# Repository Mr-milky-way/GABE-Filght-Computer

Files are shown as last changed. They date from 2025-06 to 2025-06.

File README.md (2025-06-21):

# G.A.B.E.-Filght-Computer
*Good Avionics, Bad Engineer*

## What is it?
The GABE flight computer is an open source rocket flight computer for controlling amateur or model rockets. It's a 4 layer PCB and pretty standard. It has a CoCom locked GPS, and 2 IMUs, a BMP390, 8 different servo header pins and can be powered off of a 12-26v battery. It uses and arm switch to power it on and has 6 pyro channels. It uses the MIMXRT1062DVJ6B with a teensy bootloader.



I tried to make it look nice but IDK, also that cad needs some work so thats why it's not shown.

> [!NOTE]
> The code is a demo of the Servos, LED, Pyros, and buzzer. This is so I have A low or very low ITAR risk. :)

## Why?
For aboout 3 years at this point I have wanted to make a Fin controlled rocket, and my first flight computter was, well a first. It didn't work really well and ended up frying itself via the servo PWM lines (I fixed that on this one with a level shifter). It was also large and bulky and the wire connectors were to small, not to mention it was ugly. So I set out to make this one.
I wanted it to look nice and work well and use mostly SMD parts, and for the most part I did.

## PICTURES




## BOM
Some parts have a value different from what it should be, this is because it was only one I could find. :)

| Part | Cost (all parts) | Count | Supplyer | Link | Part ID | Use | Value |
| --- | --- | ----- | --- | --- | --- | --- | --- |
| MIMXRT1062DVJ6B | $11.93 | 1 | Digikey  | [MIMXRT1062DVJ6B NXP USA Inc. \| Integrated Circuits (ICs) \| DigiKey](https://www.digikey.com/en/products/detail/nxp-usa-inc/MIMXRT1062DVJ6B/13574426) | U5 | MPU | |
| BNO055 | $12.34 | 1 | Digikey  | [BNO055 Bosch Sensortec \| Sensors, Transducers \| DigiKey](https://www.digikey.com/en/products/detail/bosch-sensortec/BNO055/6136301) | U1 | IMU | |
| TXB0108PWRG4 | $1.41 | 1 | Digikey  | [TXB0108PWRG4 Texas Instruments \| Integrated Circuits (ICs) \| DigiKey](https://www.digikey.com/en/products/detail/texas-instruments/TXB0108PWRG4/1910158) | U6 | Level Shifter | |
| RTAN0805BKE10K0 | $0.34 | 1 | Digikey  | [RTAN0805BKE10K0 Stackpole Electronics Inc \| Resistors \| DigiKey](https://www.digikey.com/en/products/detail/stackpole-electronics-inc/RTAN0805BKE10K0/6602188) | R1 | Resistor | 10KΩ |
| FC-135R 32.7680KF-A0 | $2.13 | 3 | Digikey  | [FC-135R 32.7680KF-A0 EPSON \| Crystals, Oscillators, Resonators \| DigiKey](https://www.digikey.com/en/products/detail/epson/FC-135R-32-7680KF-A0/5604247) | X1,X2,X4 | Crystal | 32.7680KHZ |
| CHV0805N250220FCT | $2.12 | 4 | Digikey  | [CHV0805N250220FCT Cal-Chip Electronics, Inc. \| Capacitors \| DigiKey](https://www.digikey.com/en/products/detail/cal-chip-electronics-inc/CHV0805N250220FCT/22155267) | C1,C2,C5,C6 | Capacitor | 22PF |
| CC0805KRX7R9BB104 | $0.48 | 6 | Digikey  | [CC0805KRX7R9BB104 YAGEO \| Capacitors \| DigiKey](https://www.digikey.com/en/products/detail/yageo/CC0805KRX7R9BB104/302874) | C3,C4,C7,C8,C11,C12 | Capacitor | 0.1UF |
| BNO085 | $13.05 | 1 | Digikey  | [BNO085 CEVA Technologies, Inc. \| Sensors, Transducers \| DigiKey](https://www.digikey.com/en/products/detail/ceva-technologies-inc/BNO085/9445940) | U2 | IMU | |
| BMP390 | $3.15 | 1 | Digikey  | [BMP390 Bosch Sensortec \| Sensors, Transducers \| DigiKey](https://www.digikey.com/en/products/detail/bosch-sensortec/BMP390/16164575) | U3 | | |
| NEO-M9N-00B | $27.00 | 1 | Digikey  | [NEO-M9N-00B u-blox \| RF and Wireless \| DigiKey](https://www.digikey.com/en/products/detail/u-blox/NEO-M9N-00B/12149174) | U4 | GPS | |
| CONSMA001-C-G | $2.79 | 1 | Digikey  | [CONSMA001-C-G TE Connectivity Linx \| Connectors, Interconnects \| DigiKey](https://www.digikey.com/en/products/detail/te-connectivity-linx/CONSMA001-C-G/11482824) | X3 | SMA connector | |
| RG0603R-330-D-T10 | $0.16 | 1 | Digikey  | [RG0603R-330-D-T10 Susumu \| Resistors \| DigiKey](https://www.digikey.com/en/products/detail/susumu/RG0603R-330-D-T10/18103232) | R2 | Resistor | 33Ω |
| BLM15PX121SN1D | $0.30 | 3 | Digikey  | [BLM15PX121SN1D Murata Electronics \| Filters \| DigiKey](https://www.digikey.com/en/products/detail/murata-electronics/BLM15PX121SN1D/4421095) | FB1-FB3 | Ferrite Bead | 120Ω |
| CC0805JRNPO9BN470 | $0.10 | 1 | Digikey  | [CC0805JRNPO9BN470 YAGEO \| Capacitors \| DigiKey](https://www.digikey.com/en/products/detail/yageo/CC0805JRNPO9BN470/302841) | C9 | Capacitor | 47PF |
| ML414H IV01E | $1.84 | 1 | Digikey  | [ML414H IV01E Seiko Instruments \| Battery Products \| DigiKey](https://www.digikey.com/en/products/detail/seiko-instruments/ML414H-IV01E/1889203) | BT1 | Battery Holder | |
| PMEG4005AEA-QX | $0.32 | 1 | Digikey  | [https://www.digikey.com/en/products/detail/nexperia-usa-inc/PMEG4005AEA-QX/17295512](https://www.digikey.com/en/products/detail/nexperia-usa-inc/PMEG4005AEA-QX/17295512) | D1 | Diode | |
| RG0603P-102-B-T10 | $0.20 | 1 | Digikey  | [RG0603P-102-B-T10 Susumu \| Resistors \| DigiKey](https://www.digikey.com/en/products/detail/susumu/RG0603P-102-B-T10/18103206) | R3 | Resistor | 1KΩ |
| C0805C105K9RACTU | $0.15 | 1 | Digikey  | [C0805C105K9RACTU KEMET \| Capacitors \| DigiKey](https://www.digikey.com/en/products/detail/kemet/C0805C105K9RACTU/2211772) | C10 | Capacitor | 1UF |
| BL-HBXJXGX32L | $0.50 | 1 | Digikey  | [BL-HBXJXGX32L American Bright Optoelectronics Corporation](https://www.digikey.com/en/products/detail/american-bright-optoelectronics-corporation/BL-HBXJXGX32L/9678124) | D2 | LED | |
| XRCGB24M000F3M00R0 | $0.30 | 1 | Digikey  | [](https://www.digikey.com/en/products/detail/murata-electronics/XRCGB24M000F3M00R0/2368376)[XRCGB24M000F3M00R0 Murata Electronics \| Crystals, Oscillators, Resonators \| DigiKey](https://www.digikey.com/en/products/detail/murata-electronics/XRCGB24M000F3M00R0/2368376) | Y1 | Crystal | 24MHZ |
| MLZ2012N4R7LT000 | $0.10 | 1 | Digikey  | [MLZ2012N4R7LT000 TDK Corporation \| Inductors, Coils, Chokes \| DigiKey](https://www.digikey.com/en/products/detail/tdk-corporation/MLZ2012N4R7LT000/2523498) | L1 | Inductor | 4.7UH |
| 112J-TDAR-R01 | $2.52 | 1 | Digikey  | [112J-TDAR-R01 ATTEND Technology \| Connectors, Interconnects \| DigiKey](https://www.digikey.com/en/products/detail/attend-technology/112J-TDAR-R01/17633874) | K1 | SD card holder | |
| BAT54CTB6_R1_00001 | $0.25 | 1 | Digikey  | [BAT54CTB6_R1_00001 Panjit International Inc. \| Discrete Semiconductor Products \| DigiKey](https://www.digikey.com/en/products/detail/panjit-international-inc/BAT54CTB6-R1-00001/15796775) | U$1 | Diode | |
| SKRPACE010 | $0.21 | 1 | Digikey  | [SKRPACE010 Alps Alpine \| Switches \| DigiKey](https://www.digikey.com/en/products/detail/alps-alpine/SKRPACE010/18115579) | S1 | Switch | |
| W25Q64JVXGIM | $1.20 | 1 | PJRC | [Bootloader Chip for DIY Teensy 4.0 & 4.1 Projects](https://www.pjrc.com/store/ic_mkl02_t4.html) | U9 | Flash Chip | |
| MKL02Z32 | $6.25 | 1 | PJRC | [Bootloader Chip for DIY Teensy 4.0 & 4.1 Projects](https://www.pjrc.com/store/ic_mkl02_t4.html) | U8 | Bootloader | |
| W25N01GVZEIG TR | $3.01 | 1 | Digikey  | [W25N01GVZEIG TR Winbond Electronics \| Integrated Circuits (ICs) \| DigiKey](https://www.digikey.com/en/products/detail/winbond-electronics/W25N01GVZEIG-TR/5803931) | U10 | Flash Chip | |
| SMTB-1240-S-R | $1.35 | 1 | Digikey  | [SMTB-1240-S-R PUI Audio, Inc. \| Audio Products \| DigiKey](https://www.digikey.com/en/products/detail/pui-audio-inc/SMTB-1240-S-R/13165906) | LS1 | Buzzer | |
| IRLML6344TRPBF | $2.10 | 6 | Digikey  | [IRLML6344TRPBF Infineon Technologies \| Discrete Semiconductor Products \| DigiKey](https://www.digikey.com/en/products/detail/infineon-technologies/IRLML6344TRPBF/2538152) | Q2-Q7 | Mosfet | |
| LM7805MPX/NOPB | $1.38 | 1 | Digikey  | [LM7805MPX/NOPB Texas Instruments \| Integrated Circuits (ICs) \| DigiKey](https://www.digikey.com/en/products/detail/texas-instruments/LM7805MPX-NOPB/6110583) | VR1 | Voltage Reguator | |
| TLV75533PDBVR | $0.32 | 1 | Digikey  | [TLV75533PDBVR Texas Instruments \| Integrated Circuits (ICs) \| DigiKey](https://www.digikey.com/en/products/detail/texas-instruments/TLV75533PDBVR/9356541) | U7 | Voltage Reguator | |
| AK100/2DS-5.0-V-GREY | $5.64 | 12 | Digikey  | [https://www.digikey.com/en/products/detail/ptr-hartmann/AK100-2DS-5-0-V-GREY/24787150](https://www.digikey.com/en/products/detail/ptr-hartmann/AK100-2DS-5-0-V-GREY/24787150) | U$2-U$13 | Terminal Block | |
| GCJ21BL8YA224KA01L | $3.52 | 11 | Digikey  | [GCJ21BL8YA224KA01L Murata Electronics \| Capacitors \| DigiKey](https://www.digikey.com/en/products/detail/murata-electronics/GCJ21BL8YA224KA01L/11618469) | C13,C14,C17,C18,C20,C23,C26,C31,C33,C34,C36 | Capacitor | .22UF |
| C0805C200J3HACAUTO | $0.26 | 2 | Digikey  | [C0805C200J3HACAUTO KEMET \| Capacitors \| DigiKey](https://www.digikey.com/en/products/detail/kemet/C0805C200J3HACAUTO/7958823) | C15,C16 | Capacitor | 20PF |
| GRM21BR61H475KE51L | $0.95 | 5 | Digikey  | [GRM21BR61H475KE51L Murata Electronics \| Capacitors \| DigiKey](https://www.digikey.com/en/products/detail/murata-electronics/GRM21BR61H475KE51L/4905540) | C19,C21,C24,C27,C30 | Capacitor | 4.7UF |
| CGA4J1X7R1V225K125AC | $0.46 | 1 | Digikey  | [CGA4J1X7R1V225K125AC TDK Corporation \| Capacitors \| DigiKey](https://www.digikey.com/en/products/detail/tdk-corporation/CGA4J1X7R1V225K125AC/2672856) | C25 | Capacitor | 2.2UF |
| CC0805KRX7R8BB103 | $0.10 | 1 | Digikey  | [CC0805KRX7R8BB103 YAGEO \| Capacitors \| DigiKey](https://www.digikey.com/en/products/detail/yageo/CC0805KRX7R8BB103/5884212) | C22 | Capacitor | 10NF |
| GRM21BR6YA106KE43L | $1.36 | 4 | Digikey  | [GRM21BR6YA106KE43L Murata Electronics \| Capacitors \| DigiKey](https://www.digikey.com/en/products/detail/murata-electronics/GRM21BR6YA106KE43L/5027598) | C28,C29,C32,C35 | Capacitor | 10UF |
| C0805C120J3GACTU | $0.44 | 2 | Digikey  | [C0805C120J3GACTU KEMET \| Capacitors \| DigiKey](https://www.digikey.com/en/products/detail/kemet/C0805C120J3GACTU/7388391) | C37,C38 | Capacitor | 12pF |
| UJ2-MIBH-G-SMT-TR | $0.44 | 1 | Digikey  | [UJ2-MIBH-G-SMT-TR Same Sky (Formerly CUI Devices) \| Connectors, Interconnects \| DigiKey](https://www.digikey.com/en/products/detail/same-sky-formerly-cui-devices/UJ2-MIBH-G-SMT-TR/13680627) | J1 | USB Con | |
| B4B-XH-A | $0.17 | 1 | Digikey  | [B4B-XH-A JST Sales America Inc. \| Connectors, Interconnects \| DigiKey](https://www.digikey.com/en/products/detail/jst-sales-america-inc/B4B-XH-A/1651047) | J2 | JST Con | |
| 61300311121 | $0.96 | 8 | Digikey  | https://www.digikey.com/en/products/detail/würth-elektronik/61300311121/4846825 | M1-M8 | Header pins | |
| DMG2305UX-7 | $0.18 | 1 | Digikey  | [DMG2305UX-7 Diodes Incorporated \| Discrete Semiconductor Products \| DigiKey](https://www.digikey.com/en/products/detail/diodes-incorporated/DMG2305UX-7/4340667) | Q1 | Mosfet | |
| SDR10EZPF2201 | $0.44 | 2 | Digikey  | [SDR10EZPF2201 Rohm Semiconductor \| Resistors \| DigiKey](https://www.digikey.com/en/products/detail/rohm-semiconductor/SDR10EZPF2201/16179905) | R4,R5 | Resistor | 2.2kΩ |
| SDR10EZPF1003 | $0.44 | 2 | Digikey  | [SDR10EZPF1003 Rohm Semiconductor \| Resistors \| DigiKey](https://www.digikey.com/en/products/detail/rohm-semiconductor/SDR10EZPF1003/17140208) | R6,R7 | Resistor | 100kΩ |
| SDR10EZPF2204 | $0.22 | 1 | Digikey  | [SDR10EZPF2204 Rohm Semiconductor \| Resistors \| DigiKey](https://www.digikey.com/en/products/detail/rohm-semiconductor/SDR10EZPF2204/19531048) | R8 | Resistor | 2.2MΩ |
| SDR10EZPF1R00 | $1.54 | 7 | Digikey  | [SDR10EZPF1R00 Rohm Semiconductor \| Resistors \| DigiKey](https://www.digikey.com/en/products/detail/rohm-semiconductor/SDR10EZPF1R00/16179859) | R9,R13,R15,R17,R19,R21,R23 | Resistor | 1Ω |
| RLT1220-F-5R00-FNH | $0.47 | 1 | Digikey  | [RLT1220-F-5R00-FNH Delta Electronics/Cyntec \| Resistors \| DigiKey](https://www.digikey.com/en/products/detail/delta-electronics-cyntec/RLT1220-F-5R00-FNH/9762198) | R10 | Resistor | 5Ω |
| RK73H2ATTD64R9F | $0.10 | 1 | Digikey  | [RK73H2ATTD64R9F KOA Speer Electronics, Inc. \| Resistors \| DigiKey](https://www.digikey.com/en/products/detail/koa-speer-electronics-inc/RK73H2ATTD64R9F/10228485?) | R11 | Resistor | 65Ω (64.9) |
| SDR10EZPF4700 | $1.32 | 6 | Digikey  | [SDR10EZPF4700 Rohm Semiconductor \| Resistors \| DigiKey](https://www.digikey.com/en/products/detail/rohm-semiconductor/SDR10EZPF4700/17140152) | R12,R14,R16,R18,R20,R22 | Resistor | 470Ω |
| RT0805BRD07723RL | $0.17 | 1 | Digikey  | [RT0805BRD07723RL YAGEO \| Resistors \| DigiKey](https://www.digikey.com/en/products/detail/yageo/RT0805BRD07723RL/7708570) | R24 | Resistor | 722Ω (723) |
| RK73H2ATTD1691F | $0.10 | 1 | Digikey  | [RK73H2ATTD1691F KOA Speer Electronics, Inc. \| Resistors \| DigiKey](https://www.digikey.com/en/products/detail/koa-speer-electronics-inc/RK73H2ATTD1691F/10234184) | R25 | Resistor | 1700Ω (1.69k) |
| COST OF MAIN PCB AND SMD-Stencil | $81.42 | 1 | PCB Way  | | | PCB | |
| TOTAL | $200.00 | 120 | | | | | |

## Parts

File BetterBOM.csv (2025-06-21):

Part | Cost (all parts) | Count | Supplyer | Link | Part ID | Use | Value
MIMXRT1062DVJ6B | $11.93 | 1 | Digikey | MIMXRT1062DVJ6B NXP USA Inc. | Integrated Circuits (ICs) | DigiKey | U5 | MPU
BNO055 | $12.34 | 1 | Digikey | BNO055 Bosch Sensortec | Sensors, Transducers | DigiKey | U1 | IMU
TXB0108PWRG4 | $1.41 | 1 | Digikey | TXB0108PWRG4 Texas Instruments | Integrated Circuits (ICs) | DigiKey | U6 | Level Shifter
RTAN0805BKE10K0 | $0.34 | 1 | Digikey | RTAN0805BKE10K0 Stackpole Electronics Inc | Resistors | DigiKey | R1 | Resistor | 10KΩ
FC-135R 32.7680KF-A0 | $2.13 | 3 | Digikey | FC-135R 32.7680KF-A0 EPSON | Crystals, Oscillators, Resonators | DigiKey | X1,X2,X4 | Crystal | 32.7680KHZ
CHV0805N250220FCT | $2.12 | 4 | Digikey | CHV0805N250220FCT Cal-Chip Electronics, Inc. | Capacitors | DigiKey | C1,C2,C5,C6 | Capacitor | 22PF
CC0805KRX7R9BB104 | $0.48 | 6 | Digikey | CC0805KRX7R9BB104 YAGEO | Capacitors | DigiKey | C3,C4,C7,C8,C11,C12 | Capacitor | 0.1UF
BNO085 | $13.05 | 1 | Digikey | BNO085 CEVA Technologies, Inc. | Sensors, Transducers | DigiKey | U2 | IMU
BMP390 | $3.15 | 1 | Digikey | BMP390 Bosch Sensortec | Sensors, Transducers | DigiKey | U3
NEO-M9N-00B | $27.00 | 1 | Digikey | NEO-M9N-00B u-blox | RF and Wireless | DigiKey | U4 | GPS
CONSMA001-C-G | $2.79 | 1 | Digikey | CONSMA001-C-G TE Connectivity Linx | Connectors, Interconnects | DigiKey | X3 | SMA connector
RG0603R-330-D-T10 | $0.16 | 1 | Digikey | RG0603R-330-D-T10 Susumu | Resistors | DigiKey | R2 | Resistor | 33Ω
BLM15PX121SN1D | $0.30 | 3 | Digikey | BLM15PX121SN1D Murata Electronics | Filters | DigiKey | FB1-FB3 | Ferrite Bead | 120Ω
CC0805JRNPO9BN470 | $0.10 | 1 | Digikey | CC0805JRNPO9BN470 YAGEO | Capacitors | DigiKey | C9 | Capacitor | 47PF
ML414H IV01E | $1.84 | 1 | Digikey | ML414H IV01E Seiko Instruments | Battery Products | DigiKey | BT1 | Battery Holder
PMEG4005AEA-QX | $0.32 | 1 | Digikey | https://www.digikey.com/en/products/detail/nexperia-usa-inc/PMEG4005AEA-QX/17295512 | D1 | Diode
RG0603P-102-B-T10 | $0.20 | 1 | Digikey | RG0603P-102-B-T10 Susumu | Resistors | DigiKey | R3 | Resistor | 1KΩ
C0805C105K9RACTU | $0.15 | 1 | Digikey | C0805C105K9RACTU KEMET | Capacitors | DigiKey | C10 | Capacitor | 1UF
BL-HBXJXGX32L | $0.50 | 1 | Digikey | BL-HBXJXGX32L American Bright Optoelectronics Corporation | D2 | LED
XRCGB24M000F3M00R0 | $0.30 | 1 | Digikey | XRCGB24M000F3M00R0 Murata Electronics | Crystals, Oscillators, Resonators | DigiKey | Y1 | Crystal | 24MHZ
MLZ2012N4R7LT000 | $0.10 | 1 | Digikey | MLZ2012N4R7LT000 TDK Corporation | Inductors, Coils, Chokes | DigiKey | L1 | Inductor | 4.7UH
112J-TDAR-R01 | $2.52 | 1 | Digikey | 112J-TDAR-R01 ATTEND Technology | Connectors, Interconnects | DigiKey | K1 | SD card holder
BAT54CTB6_R1_00001 | $0.25 | 1 | Digikey | BAT54CTB6_R1_00001 Panjit International Inc. | Discrete Semiconductor Products | DigiKey | U$1 | Diode
SKRPACE010 | $0.21 | 1 | Digikey | SKRPACE010 Alps Alpine | Switches | DigiKey | S1 | Switch
W25Q64JVXGIM | $1.20 | 1 | PJRC | Bootloader Chip for DIY Teensy 4.0 & 4.1 Projects | U9 | Flash Chip
MKL02Z32 | $6.25 | 1 | PJRC | Bootloader Chip for DIY Teensy 4.0 & 4.1 Projects | U8 | Bootloader
W25N01GVZEIG TR | $3.01 | 1 | Digikey | W25N01GVZEIG TR Winbond Electronics | Integrated Circuits (ICs) | DigiKey | U10 | Flash Chip
SMTB-1240-S-R | $1.35 | 1 | Digikey | SMTB-1240-S-R PUI Audio, Inc. | Audio Products | DigiKey | LS1 | Buzzer
IRLML6344TRPBF | $2.10 | 6 | Digikey | IRLML6344TRPBF Infineon Technologies | Discrete Semiconductor Products | DigiKey | Q2-Q7 | Mosfet
LM7805MPX/NOPB | $1.38 | 1 | Digikey | LM7805MPX/NOPB Texas Instruments | Integrated Circuits (ICs) | DigiKey | VR1 | Voltage Reguator
TLV75533PDBVR | $0.32 | 1 | Digikey | TLV75533PDBVR Texas Instruments | Integrated Circuits (ICs) | DigiKey | U7 | Voltage Reguator
AK100/2DS-5.0-V-GREY | $5.64 | 12 | Digikey | https://www.digikey.com/en/products/detail/ptr-hartmann/AK100-2DS-5-0-V-GREY/24787150 | U$2-U$13 | Terminal Block
GCJ21BL8YA224KA01L | $3.52 | 11 | Digikey | GCJ21BL8YA224KA01L Murata Electronics | Capacitors | DigiKey | C13,C14,C17,C18,C20,C23,C26,C31,C33,C34,C36 | Capacitor | .22UF
C0805C200J3HACAUTO | $0.26 | 2 | Digikey | C0805C200J3HACAUTO KEMET | Capacitors | DigiKey | C15,C16 | Capacitor | 20PF
GRM21BR61H475KE51L | $0.95 | 5 | Digikey | GRM21BR61H475KE51L Murata Electronics | Capacitors | DigiKey | C19,C21,C24,C27,C30 | Capacitor | 4.7UF
CGA4J1X7R1V225K125AC | $0.46 | 1 | Digikey | CGA4J1X7R1V225K125AC TDK Corporation | Capacitors | DigiKey | C25 | Capacitor | 2.2UF
CC0805KRX7R8BB103 | $0.10 | 1 | Digikey | CC0805KRX7R8BB103 YAGEO | Capacitors | DigiKey | C22 | Capacitor | 10NF
GRM21BR6YA106KE43L | $1.36 | 4 | Digikey | GRM21BR6YA106KE43L Murata Electronics | Capacitors | DigiKey | C28,C29,C32,C35 | Capacitor | 10UF
C0805C120J3GACTU | $0.44 | 2 | Digikey | C0805C120J3GACTU KEMET | Capacitors | DigiKey | C37,C38 | Capacitor | 12pF
UJ2-MIBH-G-SMT-TR | $0.44 | 1 | Digikey | UJ2-MIBH-G-SMT-TR Same Sky (Formerly CUI Devices) | Connectors, Interconnects | DigiKey | J1 | USB Con
B4B-XH-A | $0.17 | 1 | Digikey | B4B-XH-A JST Sales America Inc. | Connectors, Interconnects | DigiKey | J2 | JST Con
61300311121 | $0.96 | 8 | Digikey | https://www.digikey.com/en/products/detail/würth-elektronik/61300311121/4846825 | M1-M8 | Header pins
DMG2305UX-7 | $0.18 | 1 | Digikey | DMG2305UX-7 Diodes Incorporated | Discrete Semiconductor Products | DigiKey | Q1 | Mosfet
SDR10EZPF2201 | $0.44 | 2 | Digikey | SDR10EZPF2201 Rohm Semiconductor | Resistors | DigiKey | R4,R5 | Resistor | 2.2kΩ
SDR10EZPF1003 | $0.44 | 2 | Digikey | SDR10EZPF1003 Rohm Semiconductor | Resistors | DigiKey | R6,R7 | Resistor | 100kΩ
SDR10EZPF2204 | $0.22 | 1 | Digikey | SDR10EZPF2204 Rohm Semiconductor | Resistors | DigiKey | R8 | Resistor | 2.2MΩ
SDR10EZPF1R00 | $1.54 | 7 | Digikey | SDR10EZPF1R00 Rohm Semiconductor | Resistors | DigiKey | R9,R13,R15,R17,R19,R21,R23 | Resistor | 1Ω
RLT1220-F-5R00-FNH | $0.47 | 1 | Digikey | RLT1220-F-5R00-FNH Delta Electronics/Cyntec | Resistors | DigiKey | R10 | Resistor | 5Ω
RK73H2ATTD64R9F | $0.10 | 1 | Digikey | RK73H2ATTD64R9F KOA Speer Electronics, Inc. | Resistors | DigiKey | R11 | Resistor | 65Ω (64.9)
SDR10EZPF4700 | $1.32 | 6 | Digikey | SDR10EZPF4700 Rohm Semiconductor | Resistors | DigiKey | R12,R14,R16,R18,R20,R22 | Resistor | 470Ω
RT0805BRD07723RL | $0.17 | 1 | Digikey | RT0805BRD07723RL YAGEO | Resistors | DigiKey | R24 | Resistor | 722Ω (723)
RK73H2ATTD1691F | $0.10 | 1 | Digikey | RK73H2ATTD1691F KOA Speer Electronics, Inc. | Resistors | DigiKey | R25 | Resistor | 1700Ω (1.69k)
COST OF MAIN PCB AND SMD-Stencil | $81.42 | 1 | PCB Way |  |  | PCB
TOTAL | $200.00 | 120

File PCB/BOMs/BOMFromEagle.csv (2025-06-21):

Part | Value | Device | Package | Description
BT1 | RELOWABLE_BATTERY_ML414H | RELOWABLE_BATTERY_ML414H | ML414H_IV01E | SEIKO Reflowable Lithium Batteries
C1 | 22pF | 1.0UF-0805-25V-10% | 805 | ceramic capacitors
C2 | 22pF | 1.0UF-0805-25V-10% | 805 | ceramic capacitors
C3 | 0.1uF | 1.0UF-0805-25V-10% | 805 | ceramic capacitors
C4 | 0.1uF | 1.0UF-0805-25V-10% | 805 | ceramic capacitors
C5 | 22pF | 1.0UF-0805-25V-10% | 805 | ceramic capacitors
C6 | 22pF | 1.0UF-0805-25V-10% | 805 | ceramic capacitors
C7 | 0.1uF | 1.0UF-0805-25V-10% | 805 | ceramic capacitors
C8 | 0.1uF | 1.0UF-0805-25V-10% | 805 | ceramic capacitors
C9 | 47pF | 1.0UF-0805-25V-10% | 805 | ceramic capacitors
C10 | 1.0uF | 1.0UF-0805-25V-10% | 805 | ceramic capacitors
C11 | 0.1uF | 1.0UF-0805-25V-10% | 805 | ceramic capacitors
C12 | 0.1uF | 1.0UF-0805-25V-10% | 805 | ceramic capacitors
C13 | 0.22uF | 1.0UF-0805-25V-10% | 805 | ceramic capacitors
C14 | 0.22uF | 1.0UF-0805-25V-10% | 805 | ceramic capacitors
C15 | 20pF | 1.0UF-0805-25V-10% | 805 | ceramic capacitors
C16 | 20pF | 1.0UF-0805-25V-10% | 805 | ceramic capacitors
C17 | 0.22uF | 1.0UF-0805-25V-10% | 805 | ceramic capacitors
C18 | 0.22uF | 1.0UF-0805-25V-10% | 805 | ceramic capacitors
C19 | 4.7uF | 1.0UF-0805-25V-10% | 805 | ceramic capacitors
C20 | 0.22uF | 1.0UF-0805-25V-10% | 805 | ceramic capacitors
C21 | 4.7uF | 1.0UF-0805-25V-10% | 805 | ceramic capacitors
C22 | 10nF | 1.0UF-0805-25V-10% | 805 | ceramic capacitors
C23 | 0.22uF | 1.0UF-0805-25V-10% | 805 | ceramic capacitors
C24 | 4.7uF | 1.0UF-0805-25V-10% | 805 | ceramic capacitors
C25 | 2.2uF | 1.0UF-0805-25V-10% | 805 | ceramic capacitors
C26 | 0.22uF | 1.0UF-0805-25V-10% | 805 | ceramic capacitors
C27 | 4.7uF | 1.0UF-0805-25V-10% | 805 | ceramic capacitors
C28 | 10uF | 1.0UF-0805-25V-10% | 805 | ceramic capacitors
C29 | 10uF | 1.0UF-0805-25V-10% | 805 | ceramic capacitors
C30 | 4.7uF | 1.0UF-0805-25V-10% | 805 | ceramic capacitors
C31 | 0.22uF | 1.0UF-0805-25V-10% | 805 | ceramic capacitors
C32 | 10nF | 1.0UF-0805-25V-10% | 805 | ceramic capacitors
C33 | 0.22uF | 1.0UF-0805-25V-10% | 805 | ceramic capacitors
C34 | 0.22uF | 1.0UF-0805-25V-10% | 805 | ceramic capacitors
C35 | 10uF | 1.0UF-0805-25V-10% | 805 | ceramic capacitors
C36 | 0.22uF | 1.0UF-0805-25V-10% | 805 | ceramic capacitors
C37 | 12pF | 1.0UF-0805-25V-10% | 805 | ceramic capacitors
C38 | 12pF | 1.0UF-0805-25V-10% | 805 | ceramic capacitors
D1 | 0.5A/40V/420mV | DIODE-SCHOTTKY-PMEG4005EJ | SOD-323 | Schottky diode
D2 | BL-HBXJXGX32L | BL-HBXJXGX32L | LED_BL-HBXJXGX32L
FB1 | 120Ω | FERRITE_BEAD-0805-220Ω-100MHZ-2A | 805 | Ferrite Bead (blocks, cores, rings, chokes, etc.)
FB2 | 120Ω | FERRITE_BEAD-0805-220Ω-100MHZ-2A | 805 | Ferrite Bead (blocks, cores, rings, chokes, etc.)
FB3 | 120Ω | FERRITE_BEAD-0805-220Ω-100MHZ-2A | 805 | Ferrite Bead (blocks, cores, rings, chokes, etc.)
J1 | UJ2-MIBH-G-SMT-TR | UJ2-MIBH-G-SMT-TR | CUI_UJ2-MIBH-G-SMT-TR
J2 | B4B-XH-A(LF)(SN) | B4B-XH-A(LF)(SN) | JST_B4B-XH-A(LF)(SN)
K1 | 112J-TDAR-R01 | 112J-TDAR-R01 | 112J-TDAR-R01
L1 | 4.7uH | INDUCTOR-0805_WIDE-2.2UH | 0805-WIDE | Inductors
LS1 | SMTB-1240-S-R | SMTB-1240-S-R | XDCR_SMTB-1240-S-R
M1 | SERVO | SERVO | 1X03 | Servo Motor
M2 | SERVO | SERVO | 1X03 | Servo Motor
M3 | SERVO | SERVO | 1X03 | Servo Motor
M4 | SERVO | SERVO | 1X03 | Servo Motor
M5 | SERVO | SERVO | 1X03 | Servo Motor
M6 | SERVO | SERVO | 1X03 | Servo Motor
M7 | SERVO | SERVO | 1X03 | Servo Motor
M8 | SERVO | SERVO | 1X03 | Servo Motor
Q1 | MOSFET-PCHANNEL | MOSFET-PCHANNEL | SOT23-3 | Generic PMOSFET
Q2 | IRLML6344TRPBF | IRLML6344TRPBF | SOT23
Q3 | IRLML6344TRPBF | IRLML6344TRPBF | SOT23
Q4 | IRLML6344TRPBF | IRLML6344TRPBF | SOT23
Q5 | IRLML6344TRPBF | IRLML6344TRPBF | SOT23
Q6 | IRLML6344TRPBF | IRLML6344TRPBF | SOT23
Q7 | IRLML6344TRPBF | IRLML6344TRPBF | SOT23
R1 | 10k | 0.3OHM-0805-1/8W-1% | 805 | resistor
R2 | 33 | 0.3OHM-0805-1/8W-1% | 805 | resistor
R3 | 1k | 0.3OHM-0805-1/8W-1% | 805 | resistor
R4 | 2.2k | 0.3OHM-0805-1/8W-1% | 805 | resistor
R5 | 2.2k | 0.3OHM-0805-1/8W-1% | 805 | resistor
R6 | 100k | 0.3OHM-0805-1/8W-1% | 805 | resistor
R7 | 100k | 0.3OHM-0805-1/8W-1% | 805 | resistor
R8 | 2.2M | 0.3OHM-0805-1/8W-1% | 805 | resistor
R9 | 1 | 0.3OHM-0805-1/8W-1% | 805 | resistor
R10 | 5 | 0.3OHM-0805-1/8W-1% | 805 | resistor
R11 | 65 | 0.3OHM-0805-1/8W-1% | 805 | resistor
R12 | 470 | 0.3OHM-0805-1/8W-1% | 805 | resistor
R13 | 1 | 0.3OHM-0805-1/8W-1% | 805 | resistor
R14 | 470 | 0.3OHM-0805-1/8W-1% | 805 | resistor
R15 | 1 | 0.3OHM-0805-1/8W-1% | 805 | resistor
R16 | 470 | 0.3OHM-0805-1/8W-1% | 805 | resistor
R17 | 1 | 0.3OHM-0805-1/8W-1% | 805 | resistor
R18 | 470 | 0.3OHM-0805-1/8W-1% | 805 | resistor
R19 | 1 | 0.3OHM-0805-1/8W-1% | 805 | resistor
R20 | 470 | 0.3OHM-0805-1/8W-1% | 805 | resistor
R21 | 1 | 0.3OHM-0805-1/8W-1% | 805 | resistor
R22 | 470 | 0.3OHM-0805-1/8W-1% | 805 | resistor
R23 | 1 | 0.3OHM-0805-1/8W-1% | 805 | resistor
R24 | 722 | 0.3OHM-0805-1/8W-1% | 805 | resistor
R25 | 1700 | 0.3OHM-0805-1/8W-1% | 805 | resistor
S1 | SKRPACE010 | SKRPACE010 | SW_SKRPACE010
U$1 | BAT54CTB6 | BAT54CTB6 | BAT54CTB6
U$2 | AK100 | AK100 | AK100
U$3 | AK100 | AK100 | AK100
U$4 | AK100 | AK100 | AK100
U$5 | AK100 | AK100 | AK100
U$6 | AK100 | AK100 | AK100
U$7 | AK100 | AK100 | AK100
U$8 | AK100 | AK100 | AK100
U$9 | AK100 | AK100 | AK100
U$10 | AK100 | AK100 | AK100
U$11 | AK100 | AK100 | AK100
U$12 | AK100 | AK100 | AK100
U$13 | AK100 | AK100 | AK100
U1 | BNO055 | BNO055 | LGA28R50P4X10_380X520X100
U2 | BNO085 | BNO085 | IC_BNO085
U3 | BMP390L | BMP390L | XDCR_BMP390L
U4 | NEO-M9N-00B | NEO-M9N-00B | XCVR_NEO-M9N-00B
U5 | MIMXRT1062DVJ6B | MIMXRT1062DVJ6B | BGA196_MIMXRT_NXP
U6 | TXB0108PWRG4 | TXB0108PWRG4 | SOP65P640X120-20N
U7 | TLV75533PDBVR | TLV75533PDBVR | SOT95P280X145-5N
U8 | MKL02Z32VFG4QFN-16_3X3X0.65_NXP-M | MKL02Z32VFG4QFN-16_3X3X0.65_NXP-M | QFN-16_3X3X0.65_NXP-M
U9 | W25Q64JVSSIM | W25Q64JVSSIM | SOIC127P790X216-8N
U10 | W25N01GVZEIG_TR | W25N01GVZEIG_TR | SON127P800X600X80-9N
VR1 | LM7805MPX/NOPB | LM7805MPX/NOPB | VREG_LM7805MPX/NOPB
X1 |  | XTAL-3.2X1.5 | XTAL3215 | Low cost SMT crystals, no capacitors included
X2 |  | XTAL-3.2X1.5 | XTAL3215 | Low cost SMT crystals, no capacitors included
X3 | LTI-SASF54GT | LTI-SASF54GT | LTI-SASF54GT | SMA vertical PCB thrue hole jack
X4 |  | XTAL-3.2X1.5 | XTAL3215 | Low cost SMT crystals, no capacitors included
Y1 | XRCGB24M000F3M00R0 | XRCGB24M000F3M00R0 | OSC_XRCGB24M000F3M00R0

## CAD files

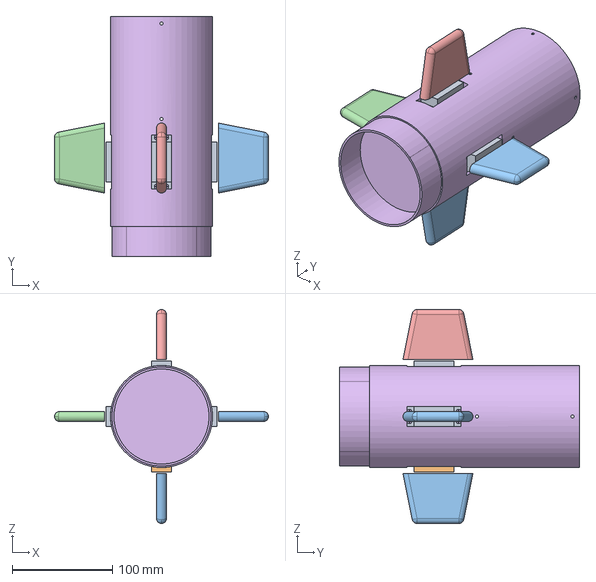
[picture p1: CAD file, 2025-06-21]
CAD/Fin_tester.step
214.0 x 240.0 x 214.0 mm

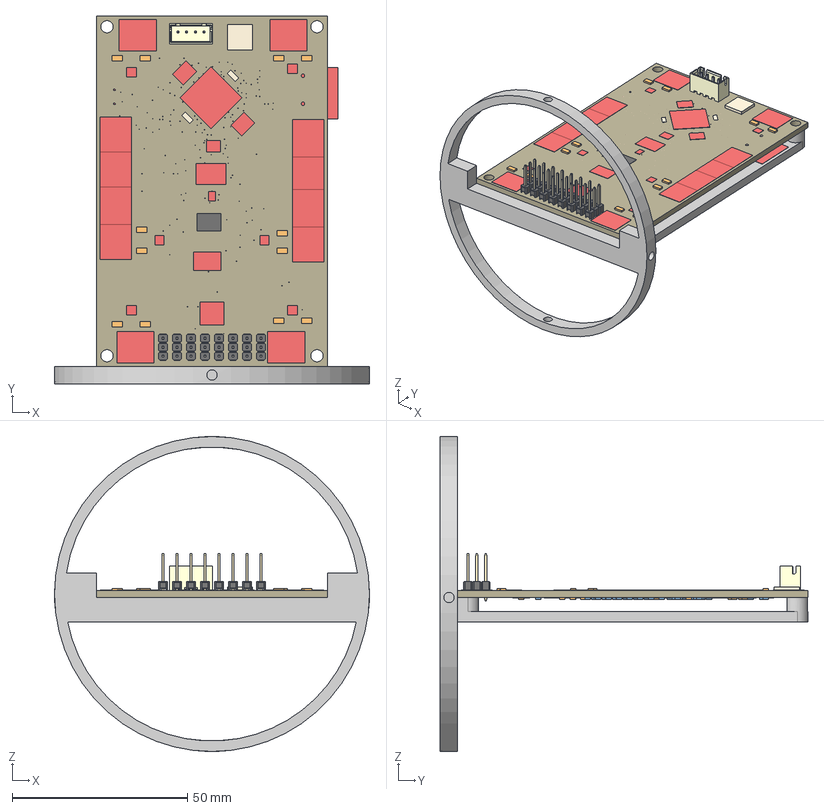
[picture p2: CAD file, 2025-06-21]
CAD/GABE_PCB_and_test_stand.step
90.0 x 105.0 x 90.0 mm
Board
BNO055
XTAL3215 x 3
BNO085
BMP390L
NEO-M9N-00B
LTI-SASF54GT
RELOWABLE_BATTERY_ML414H
0.5A/40V/420mV
12pF x 38
MIMXRT1062DVJ6B
TXB0108PWRG4
BL-HBXJXGX32L
UJ2-MIBH-G-SMT-TR
MOSFET-PCHANNEL
MKL02Z32VFG4QFN-16_3X3X0.65_NXP-M
120Ω x 3
4.7uH
112J-TDAR-R01
BAT54CTB6
SKRPACE010
W25Q64JVSSIM
W25N01GVZEIG_TR
XRCGB24M000F3M00R0
SMTB-1240-S-R
IRLML6344TRPBF x 6
AK100 x 12
LM7805MPX/NOPB
TLV75533PDBVR
B4B-XH-A (LF)(SN)
1x3 Male Pin Header x 8

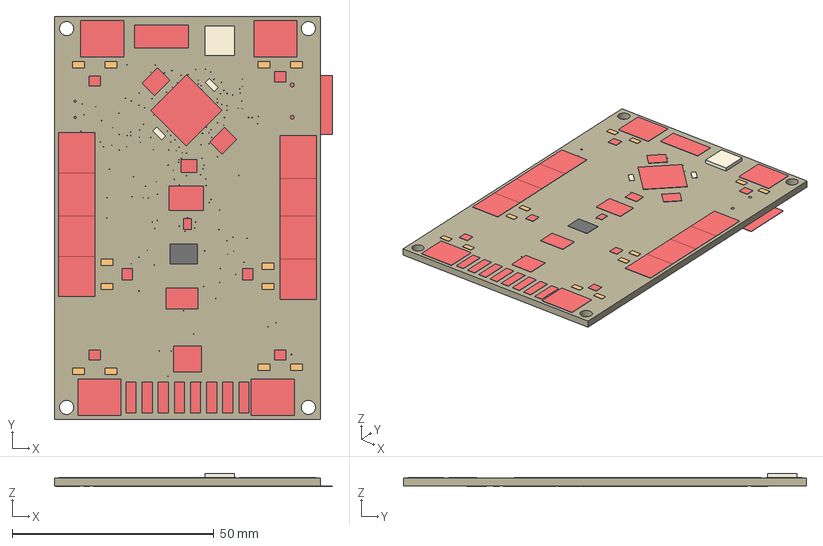
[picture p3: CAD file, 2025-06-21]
CAD/PCB.step
69.0 x 100.0 x 3.11 mm
Board
SERVO x 8
BNO055
XTAL3215 x 3
BNO085
BMP390L
NEO-M9N-00B
LTI-SASF54GT
RELOWABLE_BATTERY_ML414H
0.5A/40V/420mV
12pF x 38
MIMXRT1062DVJ6B
TXB0108PWRG4
BL-HBXJXGX32L
UJ2-MIBH-G-SMT-TR
MOSFET-PCHANNEL
MKL02Z32VFG4QFN-16_3X3X0.65_NXP-M
120Ω x 3
4.7uH
112J-TDAR-R01
BAT54CTB6
SKRPACE010
W25Q64JVSSIM
W25N01GVZEIG_TR
XRCGB24M000F3M00R0
SMTB-1240-S-R
IRLML6344TRPBF x 6
AK100 x 12
B4B-XH-A(LF)(SN)
LM7805MPX/NOPB
TLV75533PDBVR

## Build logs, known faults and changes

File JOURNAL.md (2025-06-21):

---
title: "G.A.B.E Flight Computer"
author: "Mr Milky Way"
description: "A small, multipurpose flight computer for a rocket"
created_at: "2025-05-24"
---

**Total time spent: 22h 5m**

# May 24th: Started on the PCB and BOM

I set up my repo, started to make the PCB layout and a BOM (I know there is a better way to route, but I think it looks cool)




Time Spent: 3h 31m

# May 26th: Changed PCB layout and added more to the BOM

I decided that remaking the teensy 4.1 as the fist thing was a bad idea and switched to the breakout board insted, I'm about 60% with the schematic and BOM.




Time Spent: 4h 30m

# June 4th: Started work on custom Teensy 4.1 and added a level shifter to the servo lines

I started work on remaking the teensy removed the I2C level shifter and added one to the PWM lines, I also swaped all the capacitors and resistor parts from 603 to 805.



Time Spent: 1h 34m

# June 5th: Just about done remaking the teensy

I got close to finnishing the teensy but I might change it around just to make it look nice, didn't really change the BOM that much.



# June 7th: Finished the teensy bit, and made updates to the BOM

I finished the Teensy and added mosfets, I also updated the BOM. About one hour in, I went "I'm just going to make this one with one microprocessor", this is because this is the first time I've made a board like this before (custom teensy thingy) and I only want one place where it can go wrong. If this one works well, I might make a varatint with 3 microprocessors just to make it look nice.




Time Spent: 2h 50m

# June 17th: Finished schematic, started on layout, and made small updates to the BOM

I finished the schmatic and started out on the layout, I tryed to make it look nice but ldk, just about finished the BOM.




Time Spent: 2h 26m

# June 18th: Finished the PCB.

I just finnished the PCB routing, just need to make sure it can be made with PCB-way




Time Spent: 2h 32m

# June 21th: Finished everything else and submitting.

I just finnished every thing else like the holder CAD and demo code and will be submitting this later to today


Time Spent: 2h 5m

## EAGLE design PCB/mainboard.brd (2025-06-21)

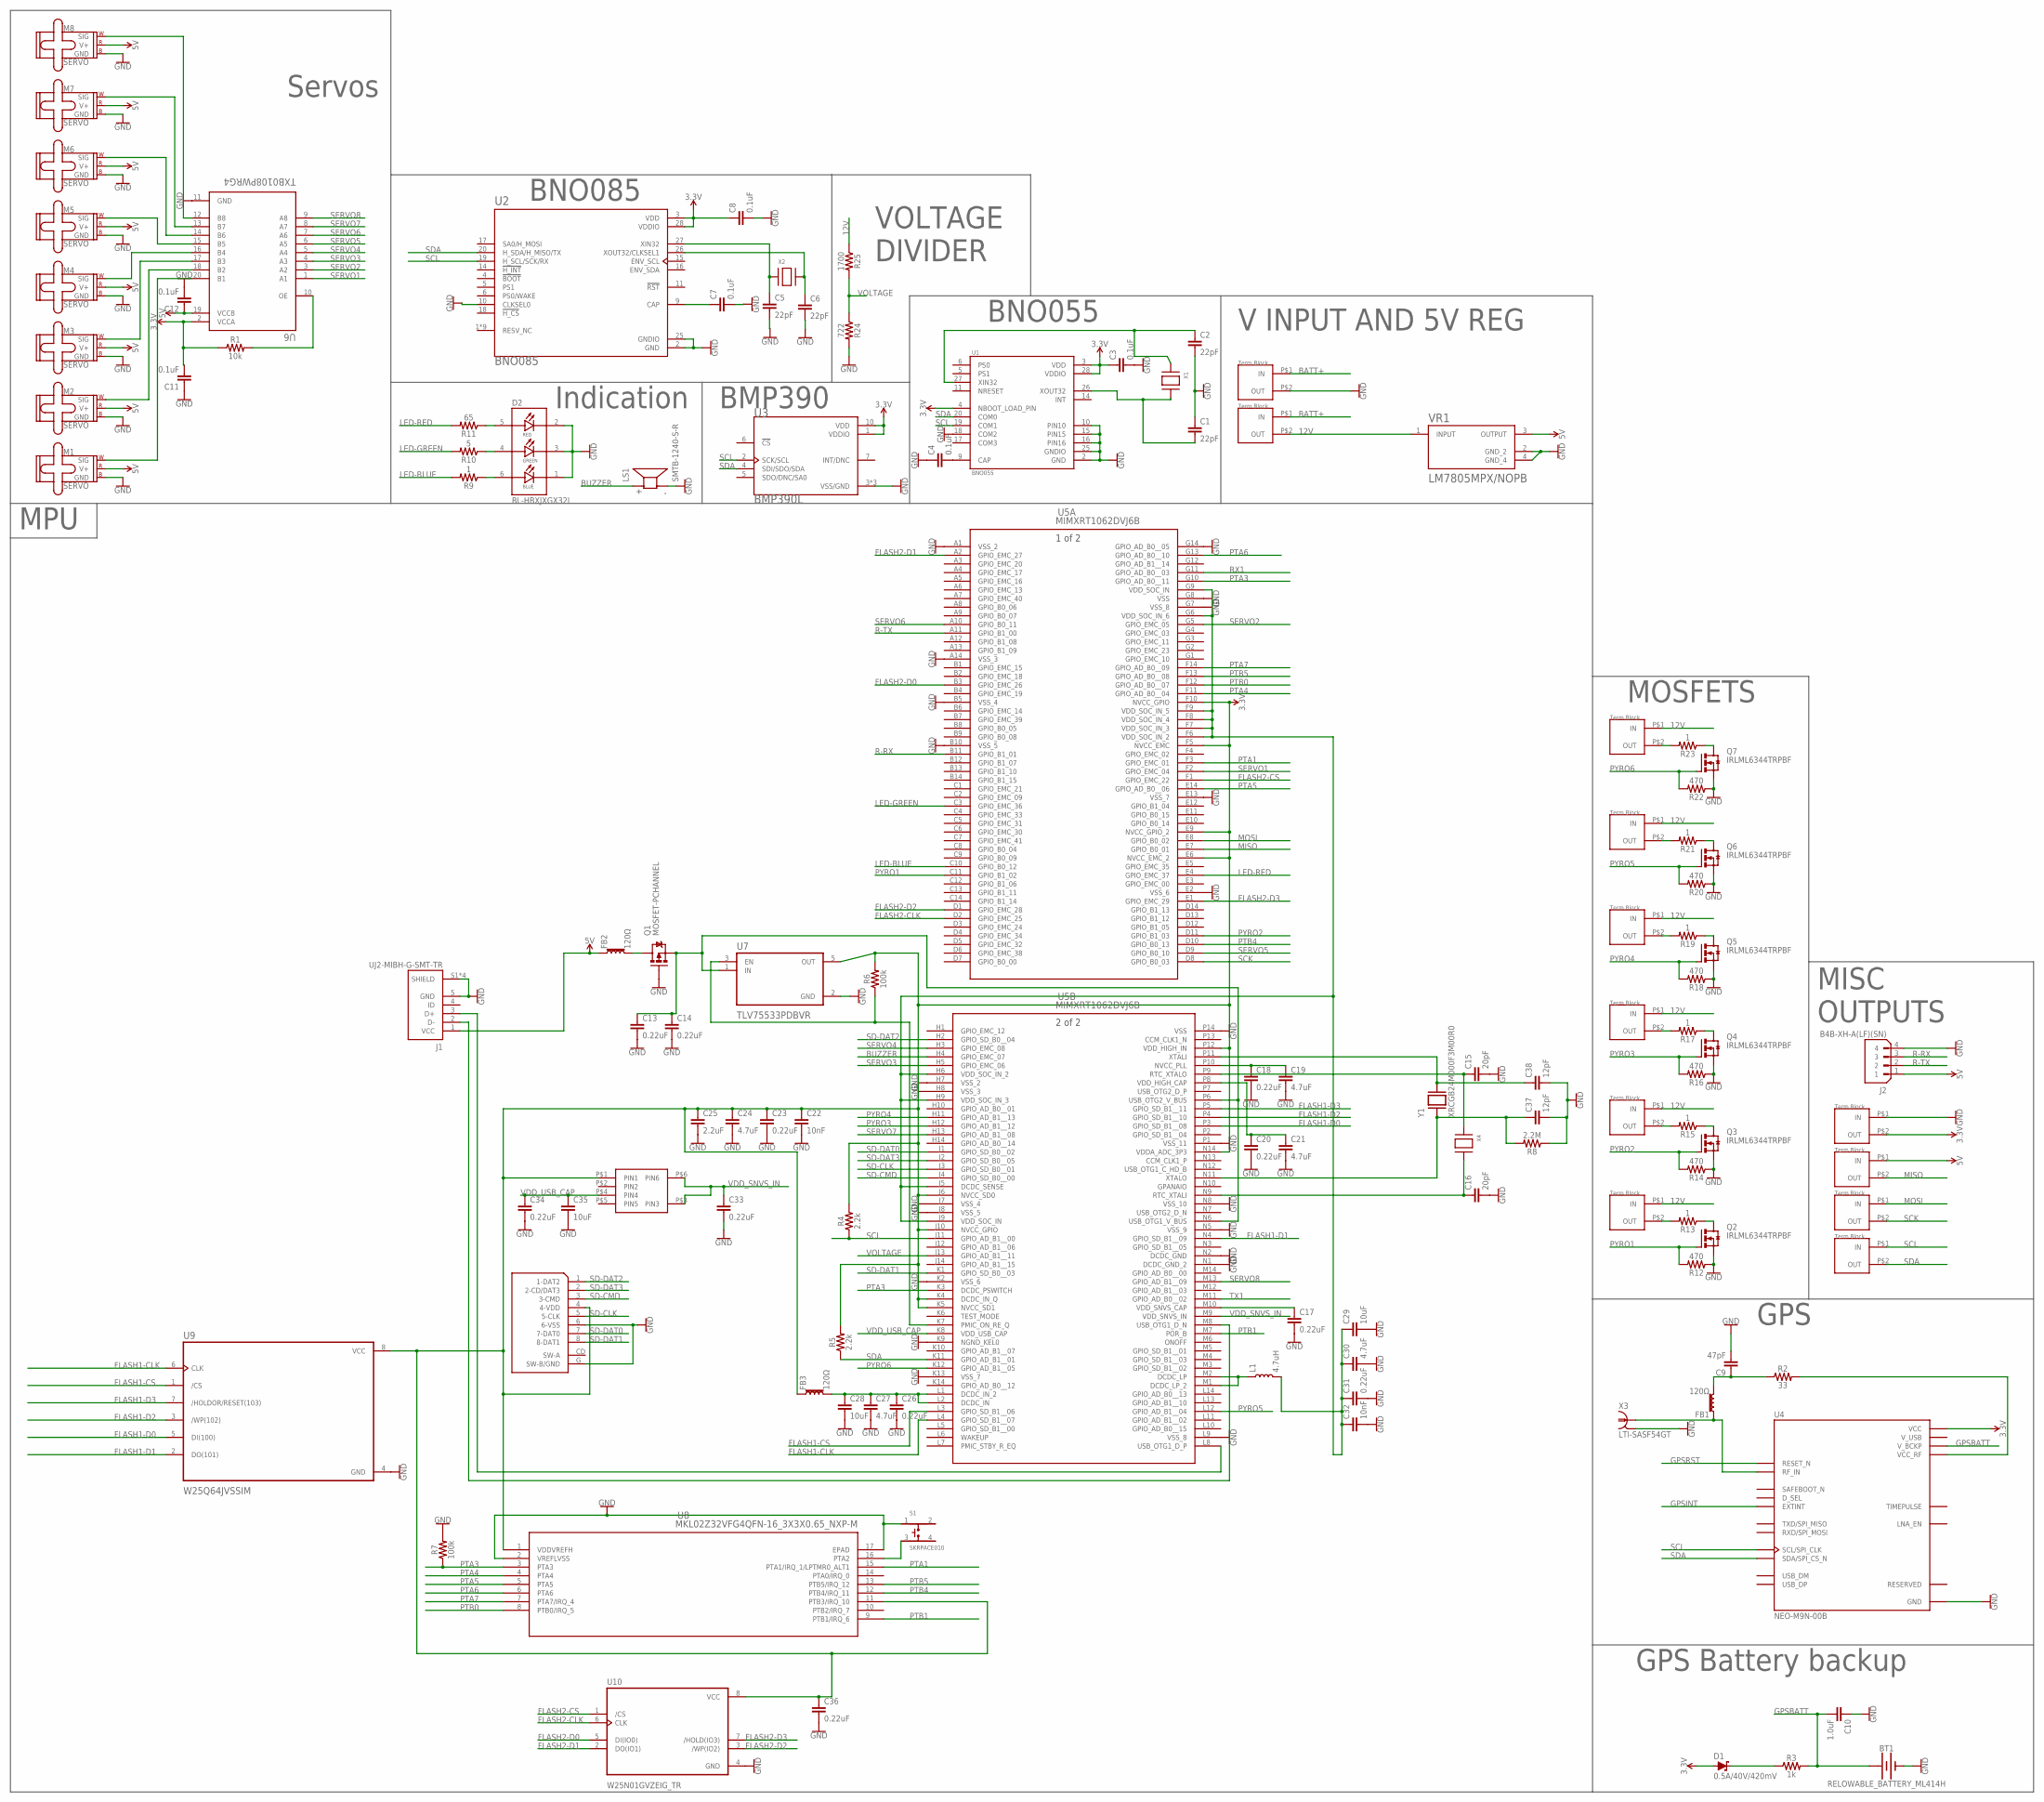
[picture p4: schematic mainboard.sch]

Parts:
BT1: RELOWABLE_BATTERY_ML414H; ML414H_IV01E
C1, C2, C5, C6: 22pF; 0805
C3, C4, C7, C8, C11, C12: 0.1uF; 0805
C9: 47pF; 0805
C10: 1.0uF; 0805
C13, C14, C17, C18, C20, C23, C26, C31, C33, C34, C36: 0.22uF; 0805
C15, C16: 20pF; 0805
C19, C21, C24, C27, C30: 4.7uF; 0805
C22, C32: 10nF; 0805
C25: 2.2uF; 0805
C28, C29, C35: 10uF; 0805
C37, C38: 12pF; 0805
D1: 0.5A/40V/420mV; SOD-323
D2: BL-HBXJXGX32L; LED_BL-HBXJXGX32L
FB1, FB2, FB3: 120Ω; 0805
J1: UJ2-MIBH-G-SMT-TR; CUI_UJ2-MIBH-G-SMT-TR
J2: B4B-XH-A(LF)(SN); JST_B4B-XH-A(LF)(SN)
K1: 112J-TDAR-R01
L1: 4.7uH; 0805-WIDE
LS1: SMTB-1240-S-R; XDCR_SMTB-1240-S-R
M1, M2, M3, M4, M5, M6, M7, M8: SERVO; 1X03
Q1: MOSFET-PCHANNEL; SOT23-3
Q2, Q3, Q4, Q5, Q6, Q7: IRLML6344TRPBF; SOT23
R1: 10k; 0805
R2: 33; 0805
R3: 1k; 0805
R4, R5: 2.2k; 0805
R6, R7: 100k; 0805
R8: 2.2M; 0805
R9, R13, R15, R17, R19, R21, R23: 1; 0805
R10: 5; 0805
R11: 65; 0805
R12, R14, R16, R18, R20, R22: 470; 0805
R24: 722; 0805
R25: 1700; 0805
S1: SKRPACE010; SW_SKRPACE010
U1: BNO055; LGA28R50P4X10_380X520X100
U2: BNO085; IC_BNO085
U3: BMP390L; XDCR_BMP390L
U4: NEO-M9N-00B; XCVR_NEO-M9N-00B
U5: MIMXRT1062DVJ6B; BGA196_MIMXRT_NXP
U6: TXB0108PWRG4; SOP65P640X120-20N
U7: TLV75533PDBVR; SOT95P280X145-5N
U8: MKL02Z32VFG4QFN-16_3X3X0.65_NXP-M; QFN-16_3X3X0.65_NXP-M
U9: W25Q64JVSSIM; SOIC127P790X216-8N
U10: W25N01GVZEIG_TR; SON127P800X600X80-9N
U$1: BAT54CTB6
U$2, U$3, U$4, U$5, U$6, U$7, U$8, U$9, U$10, U$11, U$12, U$13: AK100
VR1: LM7805MPX/NOPB; VREG_LM7805MPX/NOPB
X1, X2, X4: XTAL-3.2X1.5; XTAL3215
X3: LTI-SASF54GT
Y1: XRCGB24M000F3M00R0; OSC_XRCGB24M000F3M00R0

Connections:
3.3V: C3.1, C8.1, C11.2, C22.1, C23.1, C24.1, C25.1, C36.1, D1.A, FB3.1, K1.4 (4-VDD), R1.1, R4.2, R5.2, R6.2, U1.3 (VDD), U1.4 (NBOOT_LOAD_PIN), U1.28 (VDDIO), U2.3 (VDD), U2.28 (VDDIO), U3.1 (VDDIO), U3.10 (VDD), U4.23 (VCC), U5.E6 (NVCC_EMC_2), U5.E9 (NVCC_GPIO_2), U5.F5 (NVCC_EMC), U5.F10 (NVCC_GPIO), U5.J6 (NVCC_SD0), U5.J10 (NVCC_GPIO), U5.K4 (DCDC_IN_Q), U5.K5 (NVCC_SD1), U5.N14 (VDDA_ADC_3P3), U5.P12 (VDD_HIGH_IN), U6.2 (VCCA), U7.5 (OUT), U8.1 (VDDVREFH), U8.11 (PTB3/IRQ_10), U9.8 (VCC), U10.8 (VCC), U$1.P$1 (PIN1), U$11.P$2 (OUT)
5V: C12.1, FB2.1, J1.1 (VCC), J2.1, M1.2 (V+), M2.2 (V+), M3.2 (V+), M4.2 (V+), M5.2 (V+), M6.2 (V+), M7.2 (V+), M8.2 (V+), U6.19 (VCCB), U$10.P$1 (IN), VR1.3 (OUTPUT)
12V: R25.1, U$2.P$1 (IN), U$3.P$1 (IN), U$4.P$1 (IN), U$5.P$1 (IN), U$6.P$1 (IN), U$8.P$1 (IN), U$13.P$2 (OUT), VR1.1 (INPUT)
BATT+: U$12.P$1 (IN), U$13.P$1 (IN)
BUZZER: LS1.P (+), U5.H4 (GPIO_EMC_07)
FLASH1-CLK: U5.L4 (GPIO_SD_B1__07), U9.6 (CLK)
FLASH1-CS: U5.L3 (GPIO_SD_B1__06), U9.1 (/CS)
FLASH1-D0: U5.P3 (GPIO_SD_B1__08), U9.5 (DI(100))
FLASH1-D1: U5.N4 (GPIO_SD_B1__09), U9.2 (DO(101))
FLASH1-D2: U5.P4 (GPIO_SD_B1__10), U9.3 (/WP(102))
FLASH1-D3: U5.P5 (GPIO_SD_B1__11), U9.7 (/HOLDOR/RESET(103))
FLASH2-CLK: U5.D2 (GPIO_EMC_25), U10.6 (CLK)
FLASH2-CS: U5.F1 (GPIO_EMC_22), U10.1 (/CS)
FLASH2-D0: U5.B3 (GPIO_EMC_26), U10.5 (DI(IO0))
FLASH2-D1: U5.A2 (GPIO_EMC_27), U10.2 (DO(IO1))
FLASH2-D2: U5.D1 (GPIO_EMC_28), U10.3 (/WP(IO2))
FLASH2-D3: U5.E1 (GPIO_EMC_29), U10.7 (/HOLD(IO3))
GND: BT1.-, C1.1, C2.2, C3.2, C4.1, C5.2, C6.2, C7.2, C8.2, C9.2, C10.1, C11.1, C12.2, C13.2, C14.2, C15.2, C16.2, C17.2, C18.2, C19.2, C20.2, C21.2, C22.2, C23.2, C24.2, C25.2, C26.2, C27.2, C28.2, C29.2, C30.2, C31.2, C32.2, C33.2, C34.2, C35.2, C36.2, C37.2, C38.2, D2.1 (B_C), D2.2 (R_C), D2.3 (G_C), J1.5 (GND), J1.S1 (SHIELD), J1.S2 (SHIELD), J1.S3 (SHIELD), J1.S4 (SHIELD), J2.4, K1.6 (6-VSS), K1.G (SW-B/GND), LS1.N (-), M1.3 (GND), M2.3 (GND), M3.3 (GND), M4.3 (GND), M5.3 (GND), M6.3 (GND), M7.3 (GND), M8.3 (GND), Q1.1 (G), Q2.2 (S), Q3.2 (S), Q4.2 (S), Q5.2 (S), Q6.2 (S), Q7.2 (S), R7.2, R8.1, R12.1, R14.1, R16.1, R18.1, R20.1, R22.1, R24.2, S1.1, U1.2 (GND), U1.10 (PIN10), U1.15 (PIN15), U1.16 (PIN16), U1.18 (COM2), U1.25 (GNDIO), U2.2 (GND), U2.10 (CLKSEL0), U2.25 (GNDIO), U3.3 (VSS/GND), U3.8 (VSS/GND), U3.9 (VSS/GND), U4.10 (GND), U4.12 (GND), U4.13 (GND), U4.24 (GND), U5.A1 (VSS_2), U5.A14 (VSS_3), U5.B5 (VSS_4), U5.B10 (VSS_5), U5.E2 (VSS_6), U5.E13 (VSS_7), U5.G7 (VSS_8), U5.G8 (VSS), U5.G14 (GPIO_AD_B0__05), U5.H7 (VSS_2), U5.H8 (VSS_3), U5.J7 (VSS_4), U5.J8 (VSS_5), U5.K2 (VSS_6), U5.K9 (NGND_KEL0), U5.K13 (VSS_7), U5.L9 (VSS_8), U5.N1 (DCDC_GND_2), U5.N2 (DCDC_GND), U5.N5 (VSS_9), U5.N8 (VSS_10), U5.P1 (VSS_11), U5.P14 (VSS), U6.11 (GND), U7.2 (GND), U8.2 (VREFLVSS), U8.17 (EPAD), U9.4 (GND), U10.4 (GND), U$11.P$1 (IN), U$12.P$2 (OUT), VR1.2 (GND_2), VR1.4 (GND_4), X3.2, X3.3 (2), X3.4 (2), X3.5 (2)
GPIO_AD_B0__01: U5.H10 (GPIO_AD_B0__01)
GPIO_B1_05: U5.D12 (GPIO_B1_05)
GPIO_B1_14: U5.C14 (GPIO_B1_14)
GPIO_EMC_24: U5.D3 (GPIO_EMC_24)
GPSBATT: BT1.+, C10.2, R3.2, U4.22 (V_BCKP)
GPSINT: U4.4 (EXTINT)
GPSRST: U4.8 (RESET_N)
LED-BLUE: R9.2, U5.C10 (GPIO_B0_12)
LED-GREEN: R10.2, U5.C3 (GPIO_EMC_36)
LED-RED: R11.2, U5.E4 (GPIO_EMC_37)
MISO: U5.E7 (GPIO_B0_01), U$10.P$2 (OUT)
MOSI: U5.E8 (GPIO_B0_02), U$9.P$1 (IN)
unnamed: C2.1, U1.27 (XIN32), X1.P$1
unnamed: C1.2, U1.26 (XOUT32), X1.P$2
unnamed: C4.2, U1.9 (CAP)
unnamed: C5.1, U2.27 (XIN32), X2.P$1
unnamed: C6.1, U2.26 (XOUT32/CLKSEL1), X2.P$2
unnamed: C7.1, U2.9 (CAP)
unnamed: FB1.1, U4.11 (RF_IN), X3.1
unnamed: R2.2, U4.9 (VCC_RF)
unnamed: C9.1, FB1.2, R2.1
unnamed: D1.C, R3.1
unnamed: C16.1, U5.N9 (RTC_XTALI), X4.P$2
unnamed: R6.1, U5.K7 (PMIC_ON_RE_Q), U7.3 (EN)
unnamed: M8.1 (SIG), U6.12 (B8)
unnamed: M7.1 (SIG), U6.13 (B7)
unnamed: M6.1 (SIG), U6.14 (B6)
unnamed: M5.1 (SIG), U6.15 (B5)
unnamed: M1.1 (SIG), U6.20 (B1)
unnamed: M2.1 (SIG), U6.18 (B2)
unnamed: M3.1 (SIG), U6.17 (B3)
unnamed: M4.1 (SIG), U6.16 (B4)
unnamed: R1.2, U6.10 (OE)
unnamed: J1.2 (D-), U5.M8 (USB_OTG1_D_N)
unnamed: J1.3 (D+), U5.L8 (USB_OTG1_D_P)
unnamed: FB2.2, Q1.3 (D)
unnamed: C15.1, U5.P9 (RTC_XTALO), X4.P$1
unnamed: C13.1, C14.1, Q1.2 (S), U5.N6 (USB_OTG1_V_BUS), U5.P6 (USB_OTG2_V_BUS), U7.1 (IN)
unnamed: C26.1, C27.1, C28.1, FB3.2, U5.L1 (DCDC_IN_2), U5.L2 (DCDC_IN)
unnamed: L1.1, U5.M1 (DCDC_LP_2), U5.M2 (DCDC_LP)
unnamed: C29.1, C30.1, C31.1, C32.1, L1.2, U5.F6 (VDD_SOC_IN_2), U5.F7 (VDD_SOC_IN_3), U5.F8 (VDD_SOC_IN_4), U5.F9 (VDD_SOC_IN_5), U5.G6 (VDD_SOC_IN_6), U5.G9 (VDD_SOC_IN), U5.H6 (VDD_SOC_IN_2), U5.H9 (VDD_SOC_IN_3), U5.J5 (DCDC_SENSE), U5.J9 (VDD_SOC_IN)
unnamed: C17.1, U5.M10 (VDD_SNVS_CAP)
unnamed: C20.1, C21.1, U5.P8 (VDD_HIGH_CAP)
unnamed: C18.1, C19.1, U5.P10 (NVCC_PLL)
unnamed: S1.3, U8.16 (PTA2)
unnamed: C37.1, R8.2, U5.N11 (XTALO), Y1.1
unnamed: C38.1, U5.P11 (XTALI), Y1.3
unnamed: D2.6 (B_A), R9.1
unnamed: D2.4 (G_A), R10.1
unnamed: D2.5 (R_A), R11.1
unnamed: Q2.3 (D), R13.1
unnamed: R13.2, U$8.P$2 (OUT)
unnamed: Q3.3 (D), R15.1
unnamed: R15.2, U$2.P$2 (OUT)
unnamed: Q4.3 (D), R17.1
unnamed: R17.2, U$3.P$2 (OUT)
unnamed: Q5.3 (D), R19.1
unnamed: R19.2, U$4.P$2 (OUT)
unnamed: Q6.3 (D), R21.1
unnamed: R21.2, U$5.P$2 (OUT)
unnamed: Q7.3 (D), R23.1
unnamed: R23.2, U$6.P$2 (OUT)
PTA1: U5.F3 (GPIO_EMC_01), U8.15 (PTA1/IRQ_1/LPTMR0_ALT1)
PTA3: R7.1, U5.G10 (GPIO_AD_B0__11), U5.K3 (DCDC_PSWITCH), U8.3 (PTA3)
PTA4: U5.F11 (GPIO_AD_B0__04), U8.4 (PTA4)
PTA5: U5.E14 (GPIO_AD_B0__06), U8.5 (PTA5)
PTA6: U5.G13 (GPIO_AD_B0__10), U8.6 (PTA6)
PTA7: U5.F14 (GPIO_AD_B0__09), U8.7 (PTA7/IRQ_4)
PTB0: U5.F12 (GPIO_AD_B0__07), U8.8 (PTB0/IRQ_5)
PTB1: U5.M7 (POR_B), U8.9 (PTB1/IRQ_6)
PTB4: U5.D10 (GPIO_B0_13), U8.12 (PTB4/IRQ_11)
PTB5: U5.F13 (GPIO_AD_B0__08), U8.13 (PTB5/IRQ_12)
PYRO1: Q2.1 (G), R12.2, U5.C11 (GPIO_B1_02)
PYRO2: Q3.1 (G), R14.2, U5.D11 (GPIO_B1_03)
PYRO3: Q4.1 (G), R16.2, U5.H12 (GPIO_AD_B1__12)
PYRO4: Q5.1 (G), R18.2, U5.H11 (GPIO_AD_B1__13)
PYRO5: Q6.1 (G), R20.2, U5.L12 (GPIO_AD_B1__04)
PYRO6: Q7.1 (G), R22.2, U5.K12 (GPIO_AD_B1__05)
R-RX: J2.3, U5.B11 (GPIO_B1_01)
R-TX: J2.2, U5.A11 (GPIO_B1_00)
RX1: U5.G11 (GPIO_AD_B0__03)
SCK: U5.D8 (GPIO_B0_03), U$9.P$2 (OUT)
SCL: R4.1, U1.19 (COM1), U2.19 (H_SCL/SCK/RX), U3.2 (SCK/SCL), U4.19 (SCL/SPI_CLK), U5.J11 (GPIO_AD_B1__00), U$7.P$1 (IN)
SD-CLK: K1.5 (5-CLK), U5.J3 (GPIO_SD_B0__01)
SD-CMD: K1.3 (3-CMD), U5.J4 (GPIO_SD_B0__00)
SD-DAT0: K1.7 (7-DAT0), U5.J1 (GPIO_SD_B0__02)
SD-DAT1: K1.8 (8-DAT1), U5.K1 (GPIO_SD_B0__03)
SD-DAT2: K1.1 (1-DAT2), U5.H2 (GPIO_SD_B0__04)
SD-DAT3: K1.2 (2-CD/DAT3), U5.J2 (GPIO_SD_B0__05)
SDA: R5.1, U1.20 (COM0), U2.20 (H_SDA/H_MISO/TX), U3.4 (SDI/SDO/SDA), U4.18 (SDA/SPI_CS_N), U5.K11 (GPIO_AD_B1__01), U$7.P$2 (OUT)
SERVO1: U5.F2 (GPIO_EMC_04), U6.1 (A1)
SERVO2: U5.G5 (GPIO_EMC_05), U6.3 (A2)
SERVO3: U5.H5 (GPIO_EMC_06), U6.4 (A3)
SERVO4: U5.H3 (GPIO_EMC_08), U6.5 (A4)
SERVO5: U5.D9 (GPIO_B0_10), U6.6 (A5)
SERVO6: U5.A10 (GPIO_B0_11), U6.7 (A6)
SERVO7: U5.H13 (GPIO_AD_B1__08), U6.8 (A7)
SERVO8: U5.M13 (GPIO_AD_B1__09), U6.9 (A8)
TX1: U5.M11 (GPIO_AD_B0__02)
VDD_SNVS_IN: C33.1, U5.M9 (VDD_SNVS_IN), U$1.P$3 (PIN3), U$1.P$6 (PIN6)
VDD_USB_CAP: C34.1, C35.1, U5.K8 (VDD_USB_CAP), U$1.P$4 (PIN4)
VOLTAGE: R24.1, R25.2, U5.J13 (GPIO_AD_B1__11)
V_USB: U4.7 (V_USB)

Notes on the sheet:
Servos
GPS
GPS Battery backup
BMP390
BNO085
BNO055
MPU
Indication
MOSFETS
V INPUT AND 5V REG
MISC OUTPUTS
VOLTAGE DIVIDER

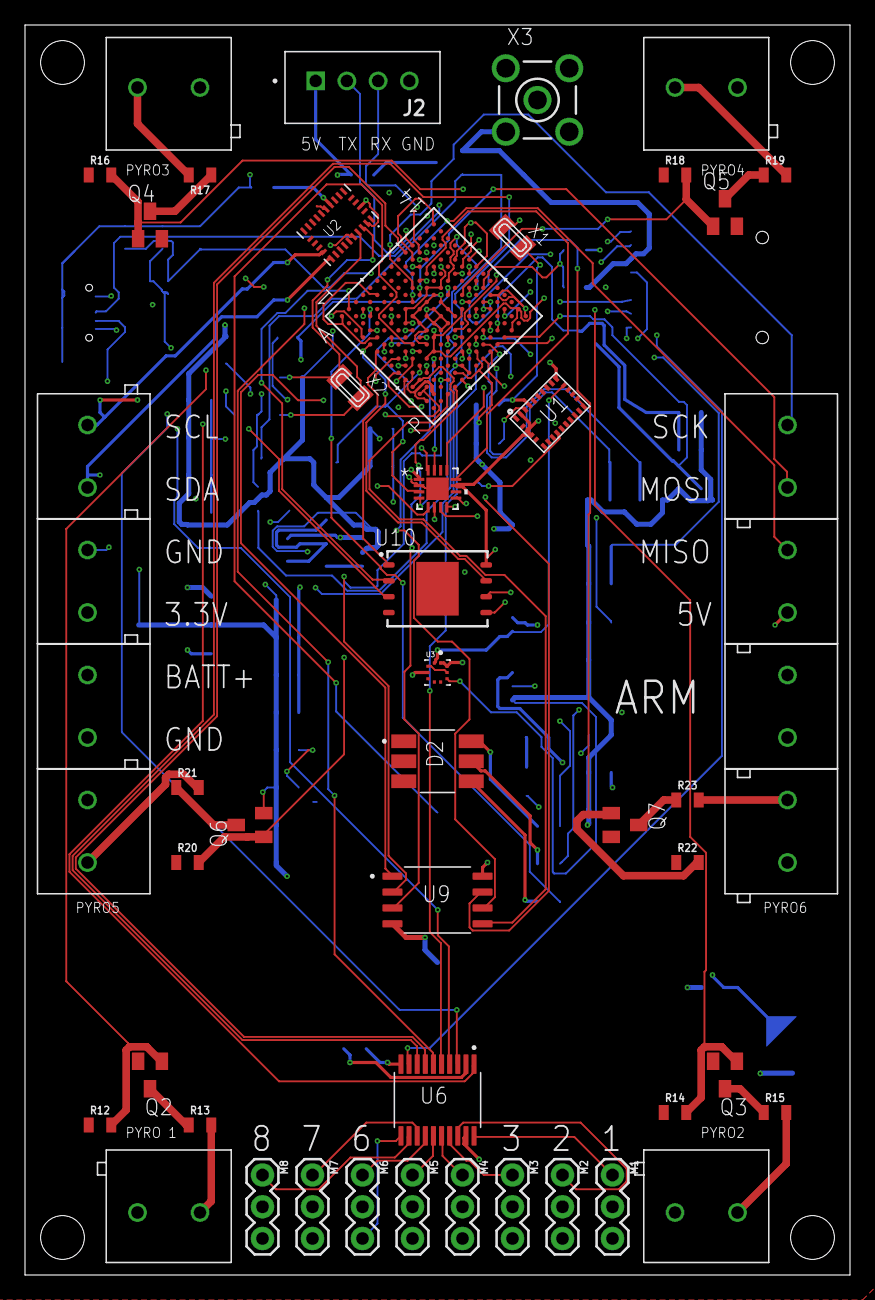
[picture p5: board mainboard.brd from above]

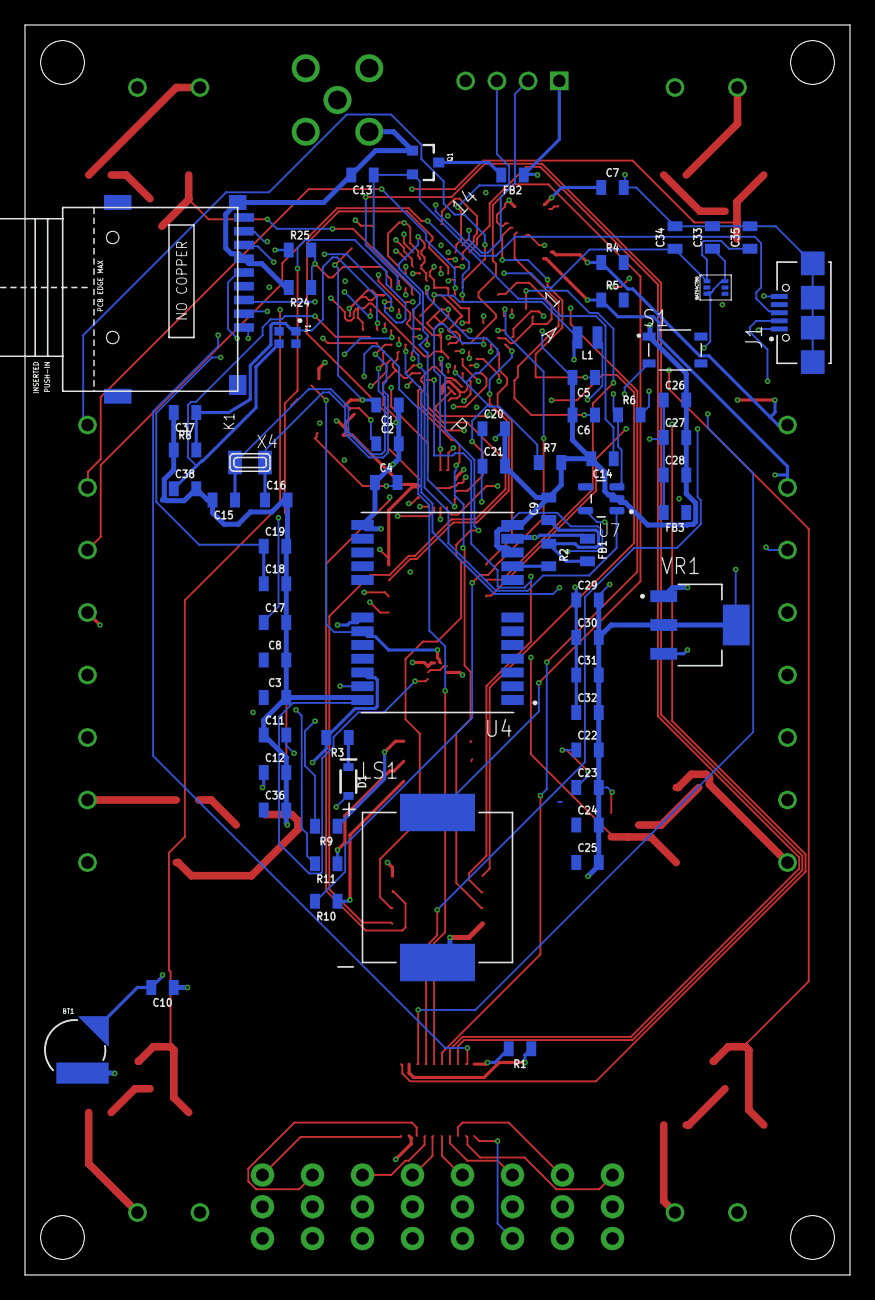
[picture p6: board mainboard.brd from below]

Board: 4 copper layers, 66.0 x 100.0 mm, 119 parts (68 on the bottom side), 112 nets.

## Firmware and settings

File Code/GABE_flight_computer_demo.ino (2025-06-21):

/* 
This is just a demo of the servos, LED, Pyros, and Buzzer.
*/

#include <PWMServo.h>

PWMServo servo1;
PWMServo servo2;
PWMServo servo3;
PWMServo servo4;
PWMServo servo5;
PWMServo servo6;
PWMServo servo7;
PWMServo servo8;


int pos = 0;
int PYRO1 = 36;
int PYRO2 = 37;
int PYRO3 = 38;
int PYRO4 = 39;
int PYRO5 = 40;
int PYRO6 = 41;
int R_LED = 30;
int B_LED = 32;
int G_LED = 31;
int buzzer = 33;

void setup() {
  Serial.begin(115200);
  Serial.write("Start up");
  pinMode(R_LED, OUTPUT);
  pinMode(B_LED, OUTPUT);
  pinMode(G_LED, OUTPUT);

  pinMode(PYRO1, OUTPUT);
  pinMode(PYRO2, OUTPUT);
  pinMode(PYRO3, OUTPUT);
  pinMode(PYRO4, OUTPUT);
  pinMode(PYRO5, OUTPUT);
  pinMode(PYRO6, OUTPUT);
  


  servo1.attach(2);
  servo2.attach(3);
  servo3.attach(4);
  servo4.attach(5);
  servo5.attach(6);
  servo6.attach(9);
  servo7.attach(22);
  servo8.attach(23);
}

void loop() {

  Serial.write("LEDs");
  digitalWrite(R_LED, LOW);
  digitalWrite(B_LED, LOW);
  digitalWrite(G_LED, LOW);
  delay(50);
  digitalWrite(R_LED, HIGH);
  digitalWrite(B_LED, LOW);
  digitalWrite(G_LED, LOW);
  delay(50);
  digitalWrite(R_LED, LOW);
  digitalWrite(B_LED, HIGH);
  digitalWrite(G_LED, LOW);
  delay(50);
  digitalWrite(R_LED, LOW);
  digitalWrite(B_LED, LOW);
  digitalWrite(G_LED, HIGH);
  delay(50);
  digitalWrite(R_LED, LOW);
  digitalWrite(B_LED, LOW);
  digitalWrite(G_LED, LOW);
  delay(50);
  digitalWrite(R_LED, HIGH);
  digitalWrite(B_LED, HIGH);
  digitalWrite(G_LED, HIGH);

  Serial.write("Servo and buzzer");
  for(pos = 0; pos < 180; pos += 1) {
    servo1.write(pos);
    servo2.write(pos);
    servo3.write(pos);
    servo4.write(pos);
    servo5.write(pos);
    servo6.write(pos);
    servo7.write(pos);
    servo8.write(pos);
    tone(buzzer, 1000);
    delay(50);
    noTone(buzzer);
  }
  for(pos = 180; pos>=1; pos-=5) {
    servo1.write(pos);
    servo2.write(pos);
    servo3.write(pos);
    servo4.write(pos);
    servo5.write(pos);
    servo6.write(pos);
    servo7.write(pos);
    servo8.write(pos);
    tone(buzzer, 1000);
    delay(50);
    noTone(buzzer);
  }
  for(pos = 0; pos < 180; pos += 10) {
    servo1.write(pos);
    servo2.write(pos);
    servo3.write(pos);
    servo4.write(pos);
    servo5.write(pos);
    servo6.write(pos);
    servo7.write(pos);
    servo8.write(pos);
    tone(buzzer, 1000);
    delay(50);
    noTone(buzzer);
  }
  for(pos = 180; pos>=1; pos-=15) {
    servo1.write(pos);
    servo2.write(pos);
    servo3.write(pos);
    servo4.write(pos);
    servo5.write(pos);
    servo6.write(pos);
    servo7.write(pos);
    servo8.write(pos);
    tone(buzzer, 1000);
    delay(50);
    noTone(buzzer);
  }

  Serial.write("Pyros");
  digitalWrite(PYRO1, LOW);
  digitalWrite(PYRO2, LOW);
  digitalWrite(PYRO3, LOW);
  digitalWrite(PYRO4, LOW);
  digitalWrite(PYRO5, LOW);
  digitalWrite(PYRO6, LOW);
  delay(1000);
  Serial.write("Pyro 1 ON");
  digitalWrite(PYRO1, HIGH);
  delay(1000);
  Serial.write("Pyro 1 OFF");
  Serial.write("Pyro 2 ON");
  digitalWrite(PYRO1, LOW);
  digitalWrite(PYRO2, HIGH);
  delay(1000);
  Serial.write("Pyro 2 OFF");
  Serial.write("Pyro 3 ON");
  digitalWrite(PYRO2, LOW);
  digitalWrite(PYRO3, HIGH);
  delay(1000);
  Serial.write("Pyro 3 OFF");
  Serial.write("Pyro 4 ON");
  digitalWrite(PYRO3, LOW);
  digitalWrite(PYRO4, HIGH);
  delay(1000);
  Serial.write("Pyro 4 OFF");
  Serial.write("Pyro 5 ON");
  digitalWrite(PYRO4, LOW);
  digitalWrite(PYRO5, HIGH);
  delay(1000);
  Serial.write("Pyro 5 OFF");
  Serial.write("Pyro 6 ON");
  digitalWrite(PYRO5, LOW);
  digitalWrite(PYRO6, HIGH);
  delay(1000);
  Serial.write("Pyro 6 OFF");
  digitalWrite(PYRO6, LOW);
}

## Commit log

2025-06-21 Added board to repo and BOM
    [BOMFromEagle.csv, BetterBOM.csv, mainboard.brd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]
2025-06-21 Added the board
    needs some work
    [PCB.step]
2025-06-21 Moved stuff into folders
    [BOMFromEagle.csv, BetterBOM.csv, PCB.step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]
2025-06-21 Added Holder
    [GABE_PCB_and_holder.step]
2025-06-21 added fintester
    [Fin_tester.step, GABE_PCB_and_test_stand.step]
2025-06-26 Fixed CAD/Code location
    [Fin_tester.step, GABE_PCB_and_test_stand.step, PCB.step]

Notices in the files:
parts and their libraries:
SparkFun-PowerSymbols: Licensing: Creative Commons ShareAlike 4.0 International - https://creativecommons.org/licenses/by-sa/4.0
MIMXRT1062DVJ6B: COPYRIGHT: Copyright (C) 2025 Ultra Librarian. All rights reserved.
